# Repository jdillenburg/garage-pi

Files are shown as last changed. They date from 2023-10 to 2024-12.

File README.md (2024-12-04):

# Deprecated
The PiZero 2W was too unreliable.  It needed to be rebooted every week and it wasn't very responsive.  For
a better version of this, see my [EspHome version](https://github.com/jdillenburg/esphome).

# Garage-Pi
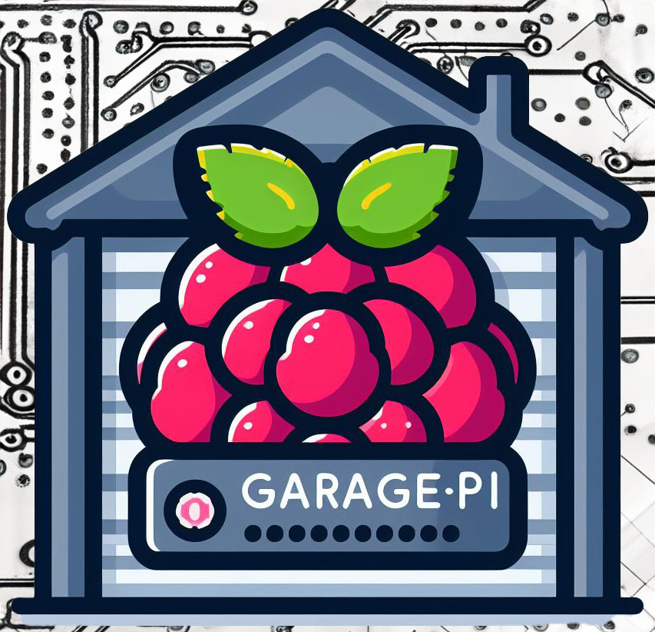
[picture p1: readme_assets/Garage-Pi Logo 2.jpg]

**by John Dillenburg (john@dillenburg.org)**

This project turns a Raspberry-Pi (3, 4, 5, or Zero-2W) into a Garage helper with features including:
* Open/Close garage door using 5V relay
* Determine Open/Close status via contact switch
* TFmini-S and Neopixel integration to display distance from car to front of garage
* [Home Assistant](https://www.home-assistant.io/) integration via MQTT 
  * Garage door device is auto-configured
  * Status of door (open/closed) and car (parked/not parked)
  * Open/close the garage door
  * Configure park distance
  * Tasker/AutoRemote integration (garage-pi pushes open/close status to AutoRemote)
* [NiceGUI](https://nicegui.io/) website
  * HTTPS and password protected
  * Open/close garage door
  * Graphs of car distance and CPU temperature
  * Scan to see if your car emits Wifi signal
  * Status of sensors
  * API end points for open/close status and control
* Option to auto-open and close based on detecting car's WiFi signal
* [Tasker](https://play.google.com/store/apps/details?id=net.dinglisch.android.taskerm) integration via [AutoRemote](https://play.google.com/store/search?q=autoremote&c=apps)
to receive open/close status and to send open/close commands

## Disclaimer
This project will be connected to your garage door opener and will be able to remotely open and close your
door using Home Assistant, via your local WiFi network, and over the Internet.  This is an obvious security concern you should weigh before starting this project.  HTTPS
and passwords are used to somewhat alleviate security concerns.  

Also, because this project is connected to your door opener's sensor and control directly, any type of power 
surge will fry the Pi and other connected components.  It wouldn't hurt to add some fuses and optical isolation
if you are worried about that.

## Screenshots
Here are some obligatory screenshots, so you can figure out if this is what you want or not.
### Home Assistant
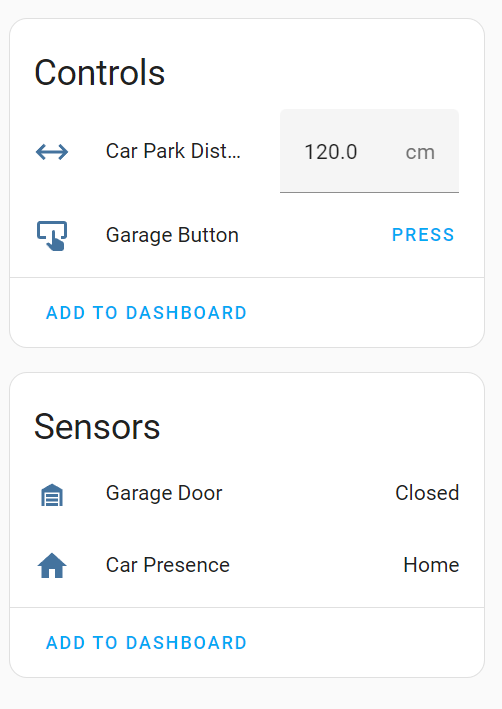
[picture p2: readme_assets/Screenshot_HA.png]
Home Assistant

### Built-In Web Site
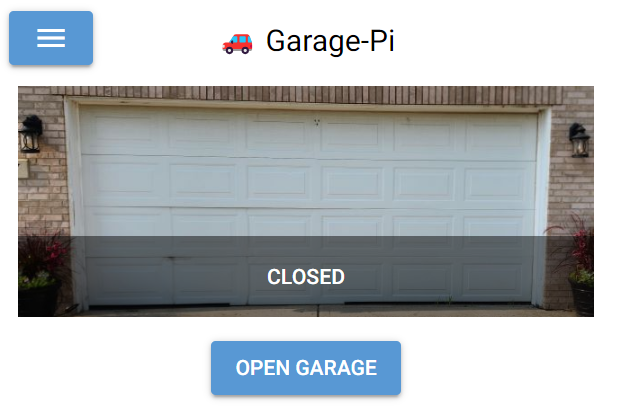
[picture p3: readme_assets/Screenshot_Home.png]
Web site homepage

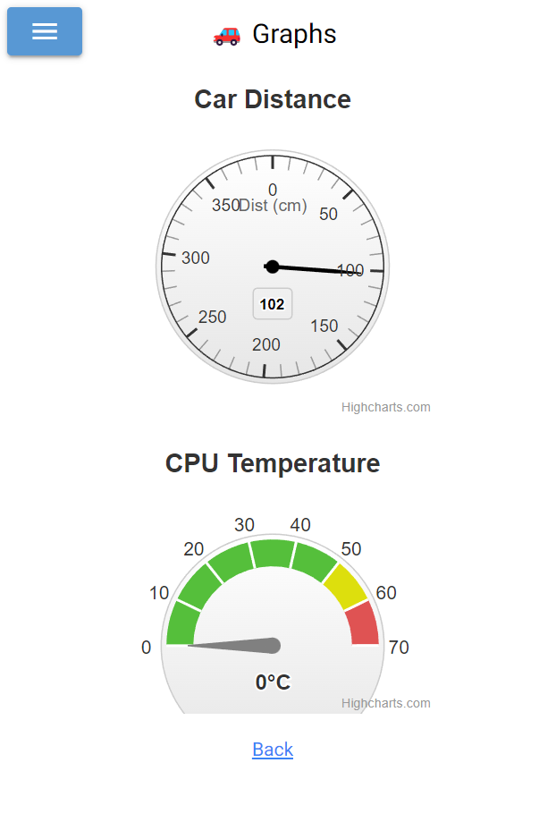
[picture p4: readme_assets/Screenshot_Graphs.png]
Graphs

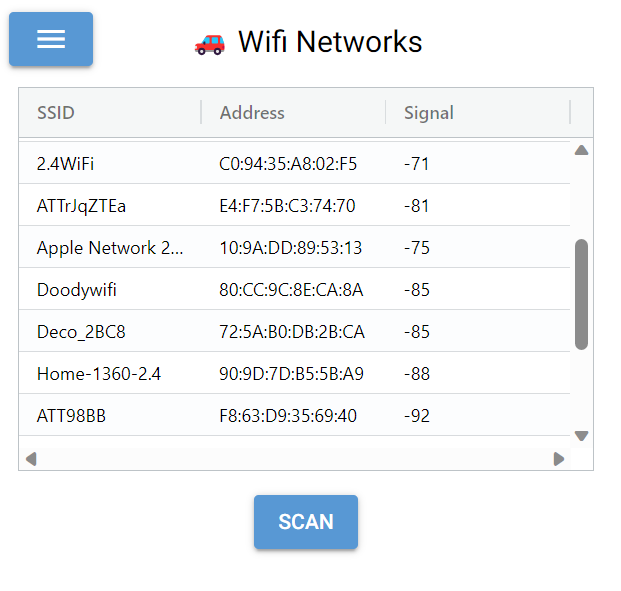
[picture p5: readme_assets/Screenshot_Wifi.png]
WiFi

## Demo
Screenshots not enough? This video shows how Garage-Pi displays the Neopixel strip of lights as a car approaches its parking distance from the front of the garage.
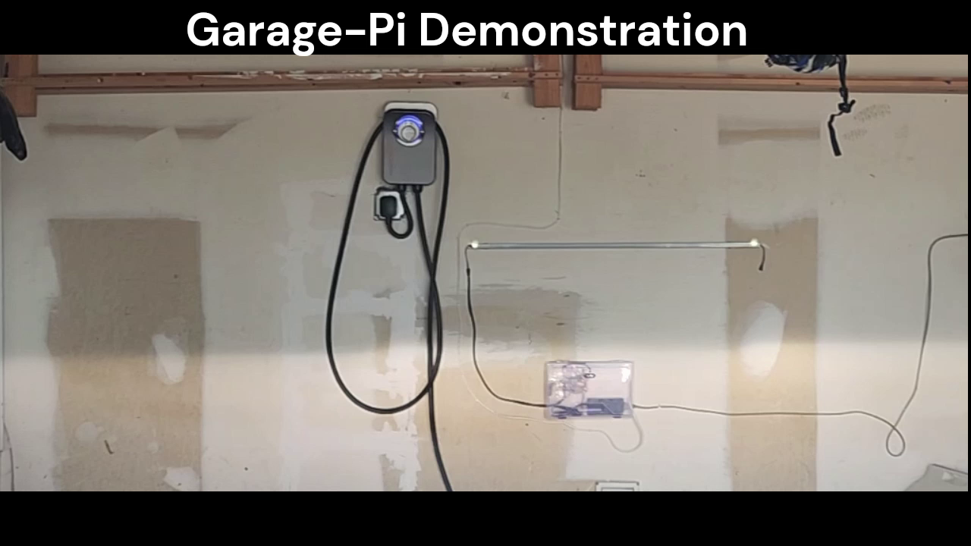
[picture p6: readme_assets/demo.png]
Garage-Pi Demo

## Command Line
If you run garage-pi with --help, the command line will be explained:
```
garage.py --help
usage: garage.py [-h] [-c CONFIG] [--ssid SSID] [--tfmini_port TFMINI_PORT] [--park_distance PARK_DISTANCE] [--max_distance MAX_DISTANCE]
                 [--neopixel_pin NEOPIXEL_PIN] [--num_pixels NUM_PIXELS] [--wlan WLAN] [--web_host WEB_HOST] [--storage_secret STORAGE_SECRET]
                 [--door_status_pin DOOR_STATUS_PIN] [--door_control_pin DOOR_CONTROL_PIN] [--mqtt_server MQTT_SERVER]
                 [--mqtt_discovery_prefix MQTT_DISCOVERY_PREFIX] [--mqtt_device_id MQTT_DEVICE_ID] [--mqtt_device_name MQTT_DEVICE_NAME]
                 [--mqtt_username MQTT_USERNAME] [--mqtt_password MQTT_PASSWORD] [--passwords PASSWORDS] [--db_file DB_FILE]
                 [--auto_open_cool_down AUTO_OPEN_COOL_DOWN] [--door_movement_delay DOOR_MOVEMENT_DELAY] [--disable_tfmini] [--disable_wifi] [--disable_web]
                 [--disable_auto_open_via_wifi] [--disable_auto_close_via_wifi] [--disable_mqtt] [--autoremote_key AUTOREMOTE_KEY]

Args that start with '--' (eg. --ssid) can also be set in a config file (/etc/garage.conf or /root/garage.conf or specified via -c). Config file syntax allows:
key=value, flag=true, stuff=[a,b,c] (for details, see syntax at https://goo.gl/R74nmi). If an arg is specified in more than one place, then commandline values
override config file values which override defaults.

optional arguments:
  -h, --help            show this help message and exit
  -c CONFIG, --config CONFIG
                        config file to load
  --ssid SSID           enable Wifi and scan for given ssid
  --tfmini_port TFMINI_PORT
                        TFmini-S port to use, defaults to /dev/ttyS0
  --park_distance PARK_DISTANCE
                        set TFmini-S park_distance to given value in centimeters, defaults to 94 cm
  --max_distance MAX_DISTANCE
                        set TFmini-S max_distance to given value in centimeters, defaults to 390 cm
  --neopixel_pin NEOPIXEL_PIN
                        Neopixel data line is connected to this pin, see Adafruit blinka library Board class
  --num_pixels NUM_PIXELS
                        number of NeoPixels, defaults to 60
  --wlan WLAN           wireless interface to use for ssid scanning, defaults to wlan0
  --web_host WEB_HOST   start web server and bind to given host
  --storage_secret STORAGE_SECRET
                        secret key for browser based storage, default is `garage-pi-4-ever`, a value is required to encrypt login)
  --door_status_pin DOOR_STATUS_PIN
                        Door status pin, passed to gpiozero Button to monitor garage door open/close status, defaults to 2
  --door_control_pin DOOR_CONTROL_PIN
                        Door control pin, passed to gpiozero OutputDevice to trigger garage door open/close relay, defaults to 17
  --mqtt_server MQTT_SERVER
                        FQDN of MQTT server to send status updates to
  --mqtt_discovery_prefix MQTT_DISCOVERY_PREFIX
                        MQTT discovery_prefix portion of topic to publish configuration and status to, defaults to homeassistant
  --mqtt_device_id MQTT_DEVICE_ID
                        MQTT device identifier to use in publications, defaults to 01ad
  --mqtt_device_name MQTT_DEVICE_NAME
                        MQTT device name to use in publications, defaults to "Garage Door"
  --mqtt_username MQTT_USERNAME
                        MQTT server username to login
  --mqtt_password MQTT_PASSWORD
                        MQTT server password to login
  --passwords PASSWORDS
                        passwords are loaded from this json file
  --db_file DB_FILE     store persistent variables in this file, defaults to garage_vars
  --auto_open_cool_down AUTO_OPEN_COOL_DOWN
                        amount of time in seconds to wait after car exits before considering opening the door, defaults to 300 seconds
  --door_movement_delay DOOR_MOVEMENT_DELAY
                        how long to wait for door to open or close before considering it a failure when door_status_pindoes not change its reading, defaults to 10
                        seconds
  --disable_tfmini      disables TFmini-S usage
  --disable_wifi        disables Wifi usage
  --disable_web         disables web interface
  --disable_auto_open_via_wifi
                        disable auto open via Wifi
  --disable_auto_close_via_wifi
                        disable auto close via Wifi
  --disable_mqtt        disables MQTT integration
  --autoremote_key AUTOREMOTE_KEY
                        Tasker auto-remote key to send garage-opened and garage-closed messages to

```
Command line options can also be saved to a file that is loaded via the --config=FILE command line option. 
```
$ cat garage.conf
ssid=My Wifi
tfmini_port=/dev/ttyS0
park_distance=104
max_distance=390
mqtt_server=homeassistant.local
mqtt_username=homeassistant
mqtt_password=password-to-your-mqtt-server
autoremote_key=Tasker-autoremote-key
$ python3 --config=garage.conf
```
By default, ~/garage.conf is loaded so if you pace garage.conf in your $HOME directory, it will be loaded by simply running garage.py:
```
$ python3 garage.py
```
## Installation
Garage-Pi requires some assembly and soldering skills in addition to software installation.  Here is a list of equipment that was used in my installation.
### Hardware Assembly
#### Parts List
(Note: Links marked "Amazon" are Affiliate links and will earn money for me.)

| Item | Price (USD) | Buy Link |
|---|---|---|
| Raspberry Pi Zero 2W | $15.00 | [SparkFun](https://www.sparkfun.com/products/18713?src=raspberrypi) |
| 32GB MicroSD Memory Card | $10.71 | [Amazon](https://www.amazon.com/gp/product/B06XWMQ81P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) |
| Raspberry Pi Zero 2W Case | $9.89 | [Amazon](https://www.amazon.com/gp/product/B075FLGWJL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) |
| 5V Relay Module 8-pack | $11.99 | [Amazon](https://www.amazon.com/gp/product/B09G6H7JDT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) |
| TFmini-S | $47.85 | [Amazon](https://www.amazon.com/gp/product/B09WDWFW21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) |
| 12V DC Fan 2-pack | $13.98 | [Amazon](https://www.amazon.com/ANVISION-Bearing-Brushless-Cooling-YDM4010B12/dp/B0711FVD48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)  |
| NeoPixel 5V LED Strip | $20.99 | [Amazon](https://www.amazon.com/gp/product/B09MVZ5DZM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) |
| 5V 5A Power Supply | $15.99 | [Amazon](https://www.amazon.com/gp/product/B08744HPRN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) | 
| Case (I used a leftover packaging box) | Free? | |
| Solderable breadboard 5-pack | $11.99 | [Amazon](https://www.amazon.com/gp/product/B07HNKJNK3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) |
| Jumper wires | $9.29 | [Amazon](https://www.amazon.com/gp/product/B077X99KX1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) |
| Capacitors 320-pack | $19.99 | [Amazon](https://www.amazon.com/gp/product/B08L5ZL87P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) |
| Logic Level Converter 3.3V->5V 10-pack | $7.39 | [Amazon](https://www.amazon.com/gp/product/B073D4DJDC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) |
| DC-DC Boost Converter 10-pack | $7.99 | [Amazon](https://www.amazon.com/gp/product/B089Y7NDCR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) |
| TOTAL | $142.21 | | 

Note that some of the above items come in packs so you will have leftover DC relays, a fan, DC boost converters, and solderable breadboards.  The total
reflects the per-item cost and not the price.
#### Circuit Diagram
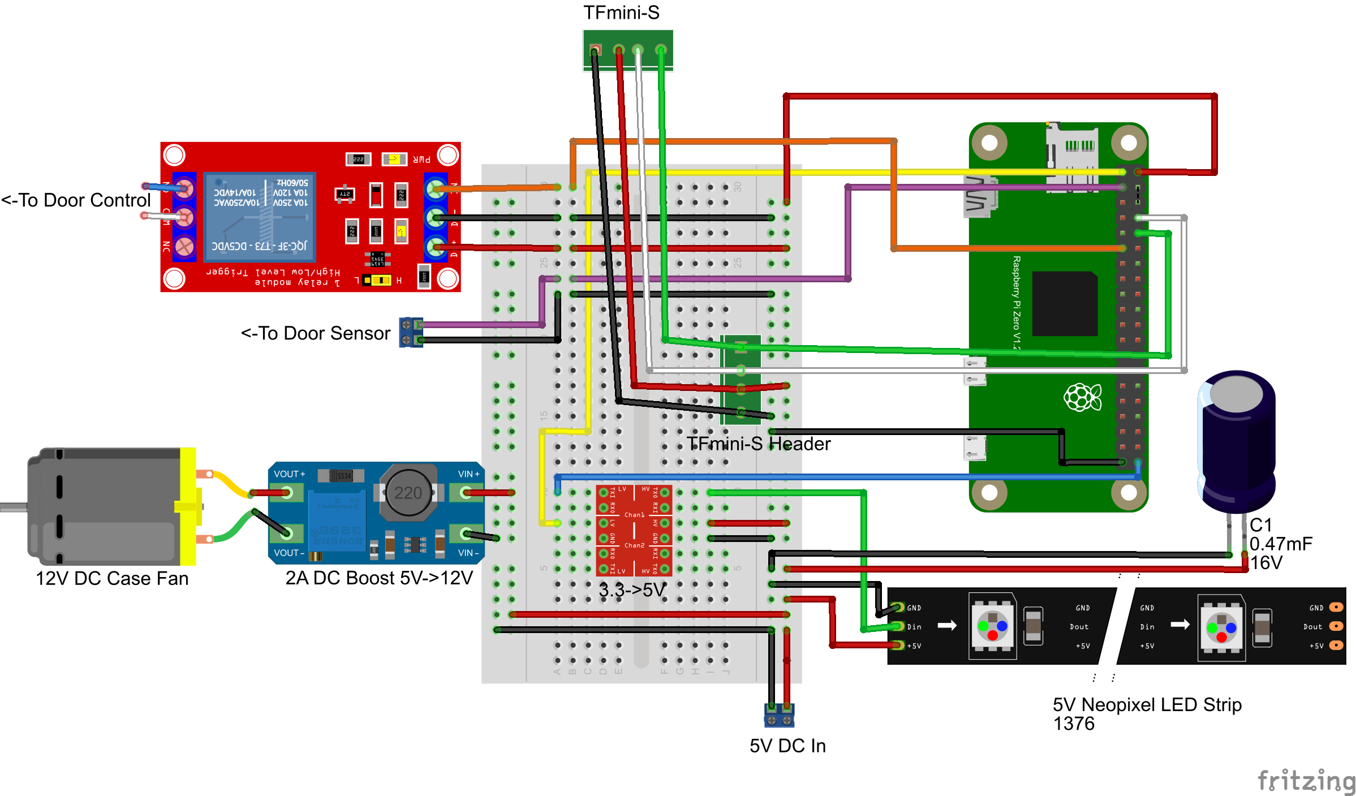
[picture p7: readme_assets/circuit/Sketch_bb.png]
Circuit Diagram


#### Raspberry Pi Zero 2W 
Although any model of Raspberry Pi will work for this project, I recommend using a Zero 2W.  Why?
I tried a Pi 4 and discovered that it overheated very easily in my garage during late July and August.
The Zero 2W is much more tolerant of the temperature extremes your garage may be subjected to.

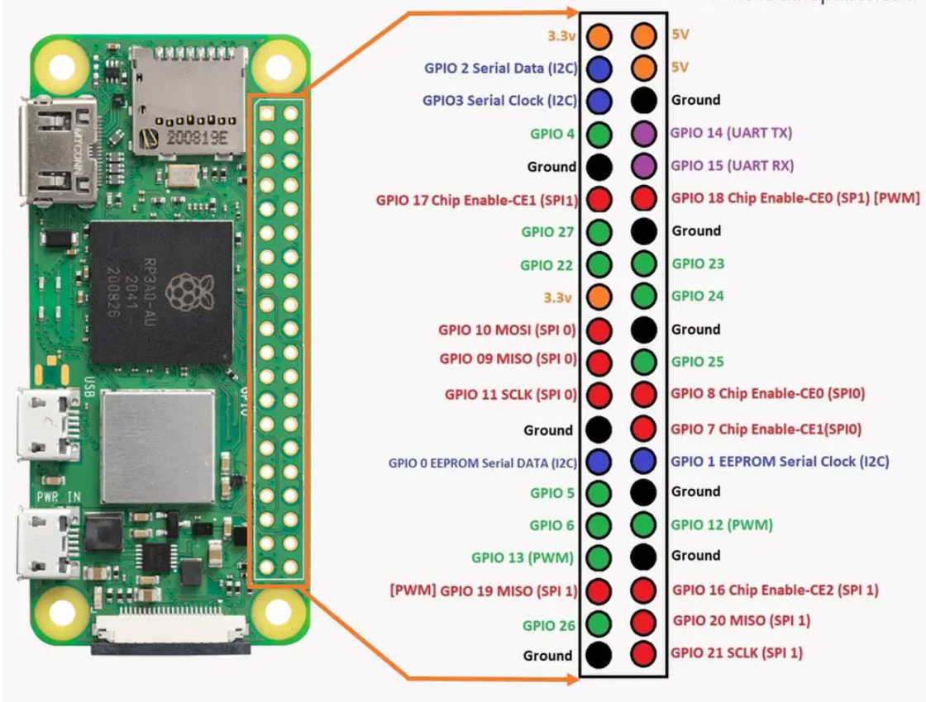
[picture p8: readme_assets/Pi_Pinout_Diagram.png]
Pi Zero 2W Pinout


Here is a table showing what the Pi pins get connected to. 

| Pi Pin | Connect To | 
|---|---|
| 3.3V | Logic Level Converter "LV" pin |
| 5V | 5V DC positive (+) |
| Ground | <ul><li>5V DC GND</li><li>NeoPixels GND</li><li>DC Boost GND</li><li>Logic Level GND</li><li>TFmini-S GND</li><li>Capacitor (-)</li><li>Control Relay GND</li><li>Sensor GND</li> |
| GPIO 14 (TX) | TFmini-S RX |
| GPIO 15 (RX) | TFmini-S TX |
| GPIO 21 | One of the Logic Level Converter TXI pins, either will do, just match up the corresponding TXO with the NeoPixel data line |
| GPIO 2 | Garage door opener's open/close sensor pin |
| GPIO 3 | Status LED positive (Optional for debugging, not used in final system) |
| GPIO 17 | Control Relay "IN" |

#### NeoPixels
Theory of operation - the NeoPixel LED strip will display the distance from the TFmini-S sensor to the vehicle entering the garage.  A vehicle that is
far away, near the end of the TFmini-S's range, will display as two pixels, one on each end of the strip.  As the vehicle approaches,
more and more LEDs will light up until the entire strip is colored in.  At this point, the lights switch to a red color to indicate that
the driver should stop the vehicle since it is located at the desired parking distance from the TFmini-S sensor. 

To connect the NeoPixels to the Raspberry Pi Zero 2W, a logic level converter is used to convert the Pi's 3.3V logic to the 
NeoPixel's 5V logic.  See below.

#### Control Relay
The 5V Control Relay is used to "push" the garage door opener's button.  This triggers the door to open or close.

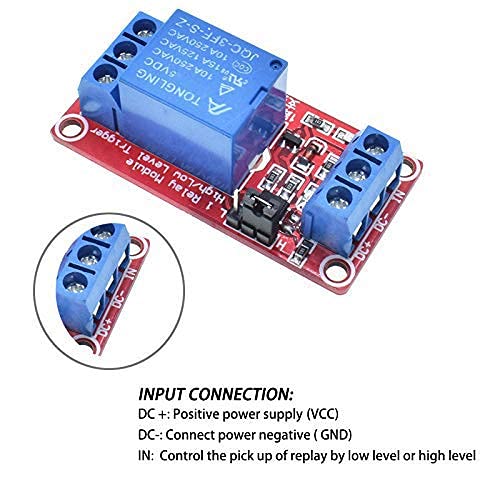
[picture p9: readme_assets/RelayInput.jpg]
Relay Input

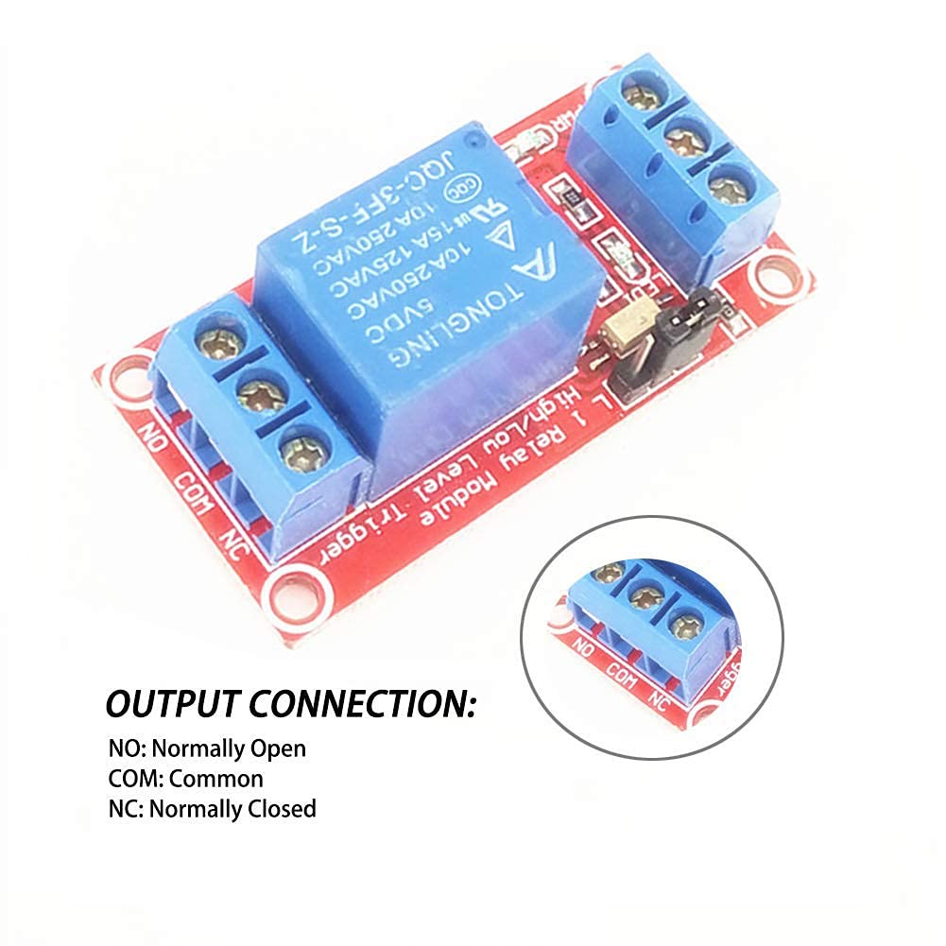
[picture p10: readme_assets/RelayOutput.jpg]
Relay Output


#### Logic Level Converter
The logic level converter is used to convert the Pi's 3.3V GPIO logic to 5V logic for the NeoPixels.

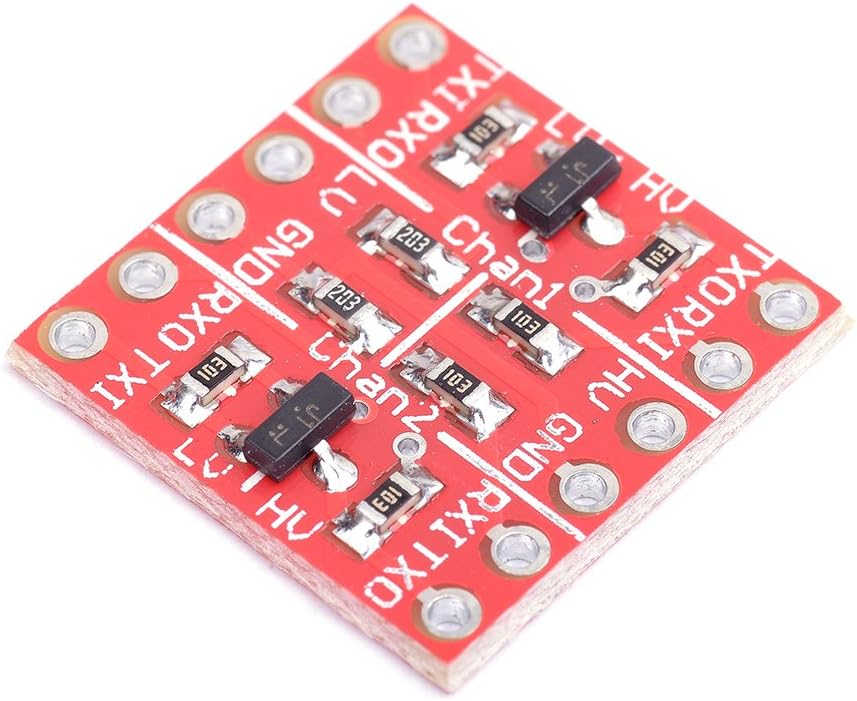
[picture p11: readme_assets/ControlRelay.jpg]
Logic Level Converter


#### TFmini-S

The "time of flight" TFmini-S is the most expensive part of this project, so you'll want to be extra careful with the
connections to it.  You probably do not want to accidentally wire up ground and +5V backwards.

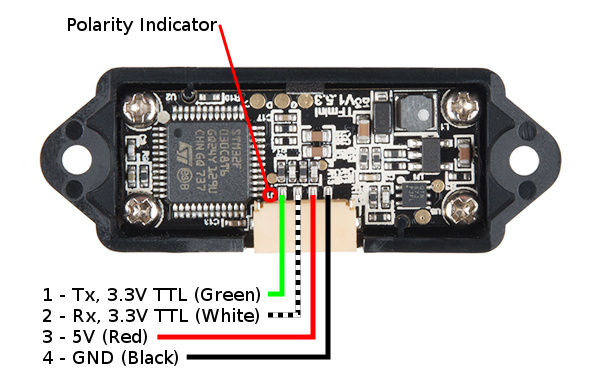
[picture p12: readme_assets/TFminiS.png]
TFmini-S


Note that I placed a generous helping of hot-melt glue on the TFmini-S connector.  It is soldered down to the 
circuit board but I found that it can easily break off while making connections and installing it on
the outside of the case.

#### Case Fan
I did end up including a case fan in this design.  This is optional since I never noticed the 2W 
overheating, even when the case fan eventually failed.  I do live in a northern climate, however, so 
make the case fan choice based on how hot your garage gets.  Also note that you could
substitute a 5V fan and forgo the 5V to 12V DC boost converter.

#### Assembled Circuit
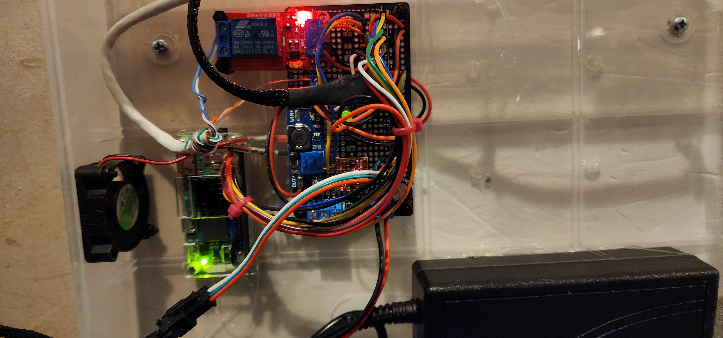
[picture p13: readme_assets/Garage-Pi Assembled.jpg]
Assembled Circuit


I screwed the solderable breadboard down to a leftover case that used to have an
assortment of screws in it.  I then screwed the case to the front wall of my garage. The TFmini-S was fastened down to the top of the case so that it faces my car as it
pulls into the garage.  THe TFmini-S is mounted at about the height of my car's bumper.

### Software
The software consists of the Raspbian operating system, some shell scripts, python code, and python libraries.
1. Write Raspbian OS to 32GB SD Card
2. Install Python
3. Install Garage-Pi
4. Configure HTTPS
5. Configure Garage-Pi 

Each of these steps will be discussed below.

#### Raspbian Operating System
You will need to use another computer to write the Raspbian OS image to the 32GB MicroSD card.  See [Raspberry Pi OS Imager](https://www.raspberrypi.com/software/).
For the O.S., choose Raspberry Pi OS (32-bit).
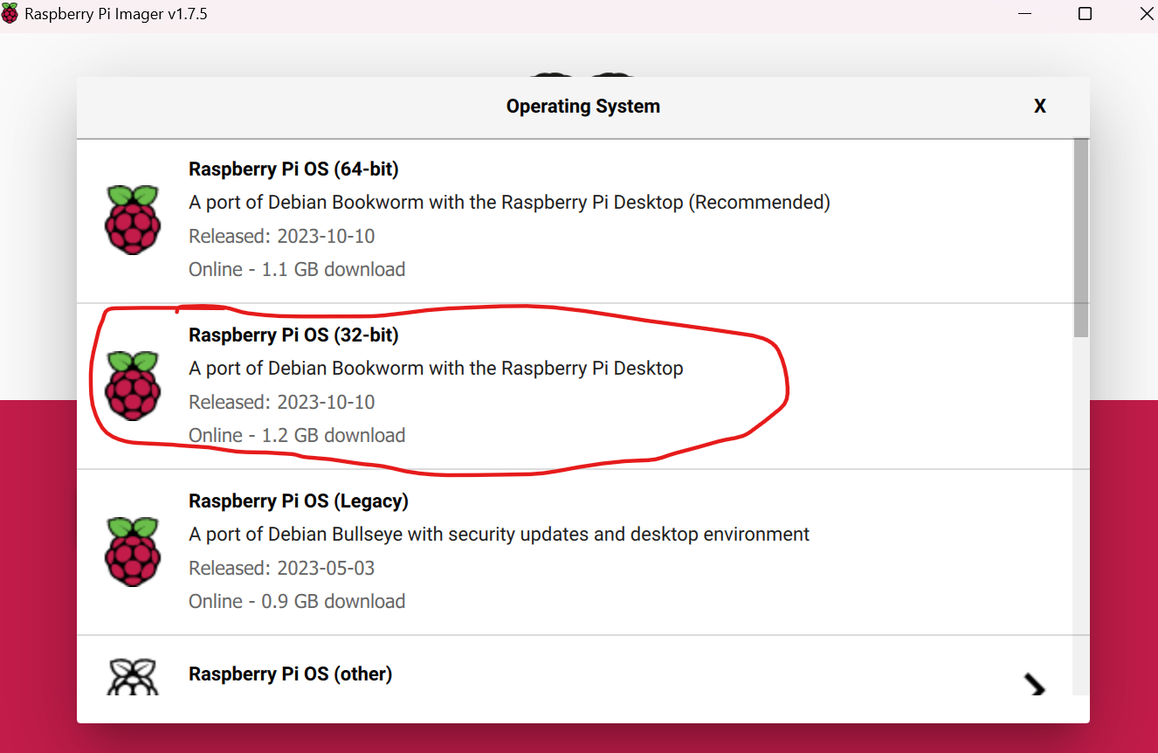
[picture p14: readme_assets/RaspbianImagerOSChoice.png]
Raspbian OS 32-bit


After you write the O.S. image to your micro-SD and insert it into the Pi, you will need to connect
a keyboard, mouse and monitor until you have remote SSH access working.

You might want to check out [SparkFun](https://learn.sparkfun.com/tutorials/getting-started-with-the-raspberry-pi-zero-2-w/all). They have a nice 
tutorial on getting started with the Raspberry Pi Zero 2W.

#### Enable WiFi on your Pi

You will need an active Internet connection to install the Garage-Pi software, Python,
and Python libraries.

To connect Raspberry Pi Zero W to WiFi, you can:
1. Use the WiFi icon on the Desktop to select and join a network ([link](https://www.bing.com/ck/a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)).
2. Edit the /etc/wpa_supplicant/wpa_supplicant.conf file and add your network name and password, then reboot your Pi ([link](https://raspberrypi.stackexchange.com/questions/68442/how-to-connect-pi-zero-w-to-the-internet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,will%20have%20to%20use%20sudo%20to%20edit%20wpa_supplicant.conf)).
3. Use the sudo iwlist wlan0 scan command to see the available networks, then edit the /etc/wpa_supplicant/wpa_supplicant.conf file and add your network name and password, then reboot your Pi ([link](https://www.bing.com/ck/a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)).

#### Python
Once your Pi is connected to the network, Python can be installed with the following commands:
```
sudo apt update
sudo apt upgrade
sudo apt install python3 -y
```
Verify that you have at least Python 3.9:
```
python -V
```

#### Garage-Pi Code
You can download the Garage-Pi code by using the 'git' command:
```
git clone https://github.com/jdillenburg/garage-pi.git
```

I like to create a virtual environment so the libraries needed do not interfere with other python programs you
may want to install later:
```
cd garage-pi
python -m venv venv
```
This creates a venv directory containing the custom python libraries we will need.
```
source venv/bin/activate
```
This switches the python and pip commands to use the venv python environment.
```
pip3 install -r requirements.txt
```
This installs the required libraries.

#### Why Sudo is Required
If you run garage.py as a normal user, then you will see the following error:
```
$ python3 garage.py
Can't open /dev/mem: Permission denied
RuntimeError: NeoPixel support requires running with sudo, please try again!
```
This is normal and is caused by the [adafruit-circuitpython-neopixel](https://github.com/adafruit/Adafruit_CircuitPython_NeoPixel) library.  You can run 
garage.py as root to avoid the error:
```
$ sudo python3 garage.py
```
This is a large security flaw, however, since we are providing an externally accessible website.
There is an explanation on the Adafruit NeoPixel page on how to use GPIO10 and raspi-config to avoid
the use of sudo.  I haven't tried this.

#### Edit passwords.json

You will need to edit the passwords.json file that comes with this code and place a username and password into it. This username and password will be needed to access the NiceGUI website on port 8080.
```
$ cat passwords.json
{"default": "changethis"}
```
You can place as many username and password pairs in the file as you like.

#### Run Garage-Pi

To start up Garage-Pi from the command line in the garage-pi directory you checked out from GitHub, simply pass
the garage.py script to python.  Don't forget to activate your Python virtual environment first:
```
source venv/bin/activate
sudo venv/bin/python3 garage.py
```
If all goes well, you should something like the following:
```
NiceGUI ready to go on http://localhost:8080, and http://127.0.1.1:8080 (install netifaces to show all IPs and speedup this message)
```
If you point a web browser at the address of your garage-pi at port 8080, you should see the login screen:

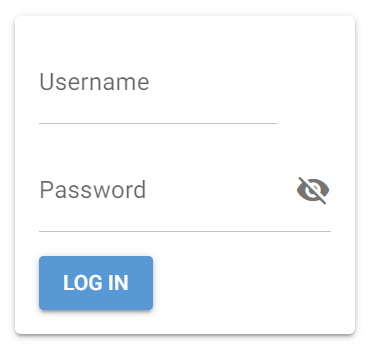
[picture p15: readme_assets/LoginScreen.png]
Login Screen


#### Enable Remote SSH Login

I'm assuming you have another computer that you can use to remotely access your garage-pi after you install
it in your garage.  You are probably will not want to keep a keyboard and monitor in your garage along with the 
Raspberry Pi.  Use the raspi-config command to enable SSH.

```
sudo raspi-config
```

Go to Interface options, SSH, then select Yes.  Make sure you can remote login before moving your 
Pi to your garage and wiring it to your door and opener.

#### Disable the Desktop Graphical User Interface

Note that the graphical desktop interface will not be needed and should be disabled using raspi-config.  I found in my testing
that the lxpanel process of the desktop GUI uses up a lot of CPU cycles.  Navigate to System Options, Boot, and select 
Console without login.

```
sudo raspi-config
```

# Acknowledgements
This system was inspired by [ResinChem Tech's](https://www.youtube.com/@ResinChemTech) "[A New Parking Assistant using ESP8266 and WS2812b LEDs](https://www.youtube.com/watch?v=HqqlY4_3kQ8)" video on YouTube.  It is an excellent system and video so I encourage you to go watch it.  His system displays the LEDs the same
way as Garage-Pi and has Home Assistant integration as well.  There is no Door or WiFi Sensors and no Door Open/Close Control, however.

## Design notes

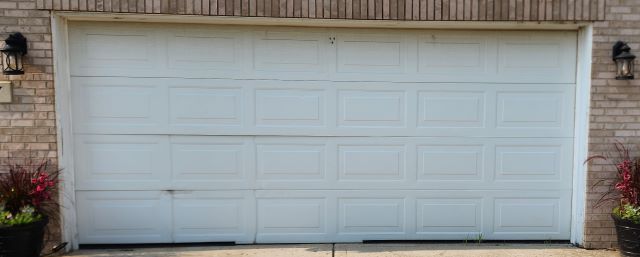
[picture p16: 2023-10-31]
static/Closed.jpg

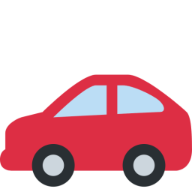
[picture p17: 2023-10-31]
static/android-chrome-192x192.png

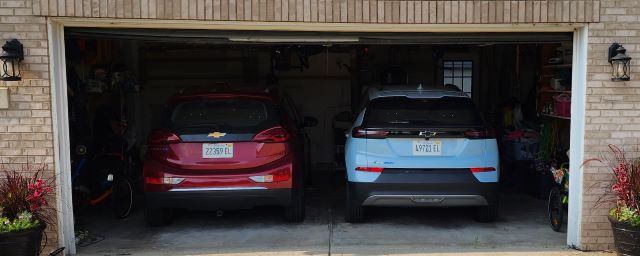
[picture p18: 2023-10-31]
static/Open.jpg

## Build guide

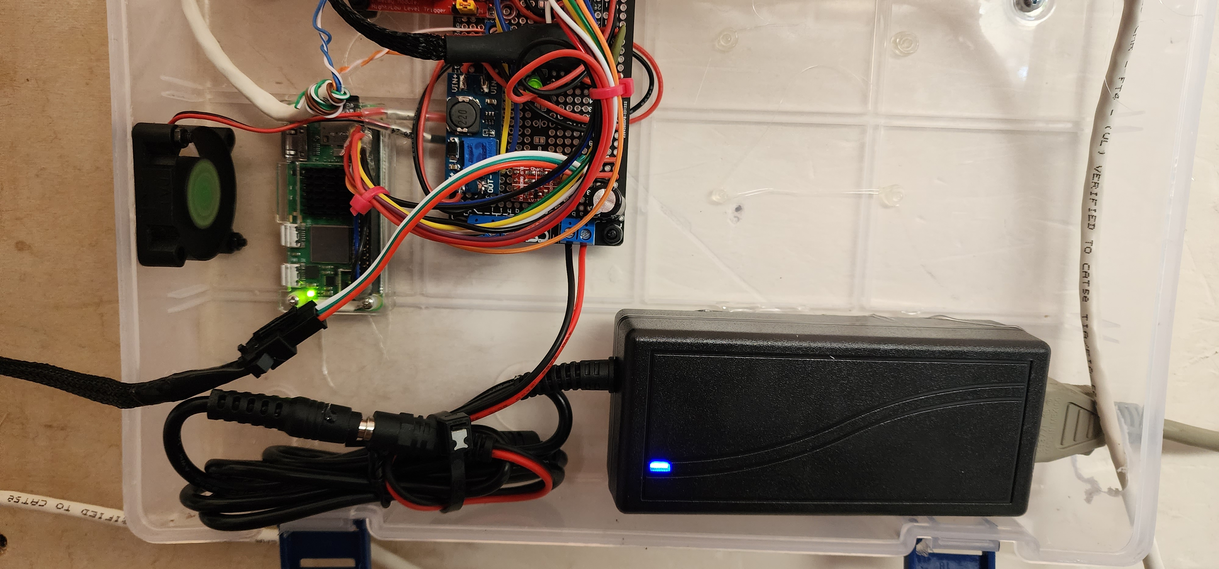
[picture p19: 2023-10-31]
readme_assets/Installation.jpg

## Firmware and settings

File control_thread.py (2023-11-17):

import logging
import time
import shelve

import board
import numpy as np

from autoremote import Autoremote
from base_thread import BaseThread
from car_status import CarStatus
from home_assistant import HomeAssistant
from home_assistant_controllable import HomeAssistantControllable
from tfminis_thread import TfminisThread
from door_control import DoorControl
from door_status_thread import DoorStatusThread, DoorStatus
from neopixel_display_thread import NeoPixelDisplayThread
from temperature_monitor_thread import TemperatureMonitorThread
from wifi_scan_thread import WifiScanThread


class ControlThread(BaseThread, HomeAssistantControllable):
    """Represents one stall of a Garage with a double door."""
    def __init__(self, park_distance: int = 94,
                 max_distance: int = 390,
                 wlan_interface: str = 'wlan0',
                 ssids: [list] = None,
                 tfmini_port: str = '/dev/ttyS0',
                 tfmini_baud: int = 115200,
                 neopixel_pin = board.D21,
                 num_pixels: int = 60,
                 door_status_pin: int = 2,
                 door_control_pin: int = 17,
                 auto_open_via_wifi: bool = True,
                 auto_close_via_wifi: bool = False,
                 mqtt_server: str = 'homeassistant.local',
                 mqtt_discovery_prefix='homeassistant',
                 mqtt_device_id='01ad',
                 mqtt_device_name='Garage Door',
                 mqtt_username: str = None,
                 mqtt_password: str = None,
                 auto_open_cool_down: int = 300,
                 db_file: str = 'garage_vars',
                 door_movement_delay:int = 10,
                 autoremote_key: str = None):
        """Create a Garage Stall control thread with the given parameters for the sensors.

        Parameters
        ----------
        park_distance - int - distance car should park at, defaults to 94
        max_distance - int - maximum distance in centimeters for TFMiniS, defaults to 390 cm
        wlan_interface - str - wifi interface used to scan for Car wifi, defaults to 'wlan0'
        ssids - list(str) - Name of car wifis to look for, defaults to None
        tfmini_port - str - TFmini-S serial port connection, defaults to /dev/ttyS0, None disables
        tfmini_baud - int - TFmini-S baud rate, defaults to 115200
        neopixel_pin - str - board.Pin for neopixel display, defaults to board.D21
        num_pixels - int - number of neopixel pins to use, defaults to 60
        door_status_pin - int - GPIOzero pin number for monitoring garage door open/close status, defaults to 2
        door_control_pin - int - GPIOzero pin number for controlling garage door via relat, defaults to 17
        auto_open_via_wifi - bool - True to use Wifi detection to open door automatically (defaults to True)
        auto_close_via_wifi - bool - True to use Wifi detection to close door automatically (defaults to False)
        mqtt_server - str - MQTT server that will receive updates to current_distance, car_parked, etc., None disables
        mqtt_discovery_prefix - str - prefix for mqtt topic so that homeassistant can see it, defaults to 'homeassistant'
        mqtt_device_id - str - device identifier to use in publications to MQTT, defaults to '01ad'
        mqtt_device_name - str - device name to use in publications to MQTT, defaults to 'Garage Door'
        mqtt_username - str - username to login to MQTT server with, defaults to None meaning no user/password required
        mqtt_password - str - password needed to login to MQTT server, defaults to None meaning no password needed
        auto_open_cool_down - int - number of seconds to wait after exiting before auto-opening garage when Wifi is
            seen, defaults to 300 (5 minutes)
        db_file - str - name of file to use for storage of persistent variables last_found, last_not_found, etc,
            defaults to 'garage_vars' (.db is auto-appended)
        door_movement_delay - int - number of seconds to wait before considering open or close a failure if
            door_status_pin does not change, defaults to 10 seconds
        autoremote_key - str - Tasker autoremote key to send garage-opened and garage-closed messages to
        """
        super(ControlThread, self).__init__()
        self.max_distance = max_distance
        self.park_distance = park_distance
        if tfmini_port is not None:
            self.tfminis = TfminisThread(port=tfmini_port, baud=tfmini_baud)
        else:
            self.tfminis = None
            logging.info('TFmini-S disabled')
        self.wlan_interface = wlan_interface
        self.ssids = ssids
        self.display = NeoPixelDisplayThread(max_distance = max_distance, pin=neopixel_pin, num_pixels=num_pixels)
        self.door_status = DoorStatusThread(gpio_pin=door_status_pin, door_movement_delay=door_movement_delay)
        if autoremote_key is not None:
            self.autoremote = Autoremote(autoremote_key)
        else:
            self.autoremote = None
        self.control = DoorControl(gpio_pin=door_control_pin)
        if mqtt_server is not None:
            self.home_assistant = HomeAssistant(self,
                                                mqtt_server=mqtt_server,
                                                mqtt_discovery_prefix=mqtt_discovery_prefix,
                                                mqtt_device_id=mqtt_device_id,
                                                mqtt_device_name=mqtt_device_name,
                                                mqtt_username=mqtt_username,
                                                mqtt_password=mqtt_password
                                                )
        else:
            self.home_assistant = None
        # readings array will have time in column 0 and distance in column 1
        self.readings = np.zeros((0,2))
        self.readings_size_in_seconds = 5.0
        self.speed = 0.0
        if ssids is not None and self.wlan_interface is not None:
            self.wifi_scanner = WifiScanThread(self.ssids, self.wlan_interface)
        else:
            self.wifi_scanner = None
            logging.info('Wifi scanner disabled')
        self.current_distance = 0.0
        self.temperature_monitor = TemperatureMonitorThread()
        self.auto_open_via_wifi = auto_open_via_wifi
        self.auto_close_via_wifi = auto_close_via_wifi
        self.auto_open_cool_down = auto_open_cool_down # seconds
        self.db = shelve.open(db_file, writeback=True)
        if 'last_found' not in self.db:
            self.db['last_found'] = 0
            self.db['last_not_found'] = 0
            self.db['last_parked'] = 0
            self.db['last_exiting'] = 0
            self.db['last_entering'] = 0
            self.db['car_status'] = CarStatus.UNKNOWN
            self.db.sync()
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

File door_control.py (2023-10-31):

from gpiozero import OutputDevice
import time
import logging

class DoorControl:
    """Simple class that encapsulates the pressing of the garage door control button.  Uses
    the gpiozero library to control a 5V rely on a GPIO pin of the raspberry pi (defaults to 17)."""
    
    def __init__(self, gpio_pin = 17):
        self.gpio_pin = gpio_pin
        self.output = OutputDevice(gpio_pin)
        self.listeners = list()
        self.last_pressed = 0
        
    def press(self):
        if time.time() - self.last_pressed > 1.0:
            logging.warning('triggering open/close button')
            self.last_pressed = time.time()
            self.output.on()
            time.sleep(0.1)
            self.output.off()
            for listener in self.listeners:
                listener(self)
        else:
            logging.warning('attempt to press control button too often is ignored')

    def close(self):
        self.output.close()

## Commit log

2023-11-01 Added jumper wires to parts list.
2023-11-01 Assembled circuit section mopved
2023-11-03 Add links to HA, NiceGUI and Tasker. Add board library to requirements.txt
2023-11-17 Fixed memory leak. Added "Disable GUI" section to README.md.
    [control_thread.py]
